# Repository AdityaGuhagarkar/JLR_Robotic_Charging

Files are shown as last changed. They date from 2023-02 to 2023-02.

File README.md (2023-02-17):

# JLR_Robotic_Charging

<!-- PROJECT DESCRIPTION -->

## Introduction:
The objective of this project was to develop a robotic arm that can automatically detect the vehicle's charging port and plug the socket into the charging port.

## Methodology:
<p>◦The CAD model of the robotic arm was developed using Fusion360 and SolidWorks. The Robotic arm simulation was done on MATLAB using the Kinova Gen3 Model for testing arm control algorithms.</p>
<p>◦For perception, a Yolov7 model was trained to detect the CCS2 charging port. Then, stereo cameras were used to determine the distance to the charding port. Finally an Aruco marker placed near the charging port was used to obtain the 6D pose.</p>
<p>◦For the given end pose, we create an inverse kinematics solver. To solve the inverse kinematics for each waypoint, we first obtain the target pose as a function of the waypoints and their orientations. The joint waypoints are then defined via the inverse kinematics function.</p>
<p>◦We have defined 4 ways to generate a trajectory, namely ‘trap’, ‘cubic’, ‘quintic’, and ‘bspline’</p>
<p>◦Then, we plot Velocity vs Time, Acceleration vs Time, Torque vs Time and Power vs Time via which we can find average power.</p>
<p>◦Torque is defined using the inverseDynamics function with the pose, velocity, acceleration and external forces as variables.</p>
<p>◦We finally visualize the robotic arm motion on a 3D plot</p>

## Robot Arm Design:

Objective:
To design a robotic arm that should be able to reach the charging port of the electric vehicle from the charging station with all the constraints as stated

Approach:
<p>Two different approaches have been taken to achieve the said objective</p>
◦Design_1: Design of a 6-DOF robotic arm <br>
◦Design_2 (alternate approach): Design of a 6-DOF robotic arm using pneumatically controlled artificial muscles for tough robotic applications <br>
<br>
<p>Design Specifications:</p>
◦DOF: 6 <br>
◦Mass: 54.2 kg <br>
◦Bounding box dimension: 0.16*0.7*0.17 (m) <br>
◦Payload: 5 kg <br>
◦Max. reach: 1.42 m <br>
◦Material: Al 6061 T6, PLA (3D printed shells for motor casing) <br>
<br>
MAIN MODEL
<br>
<p align="center">
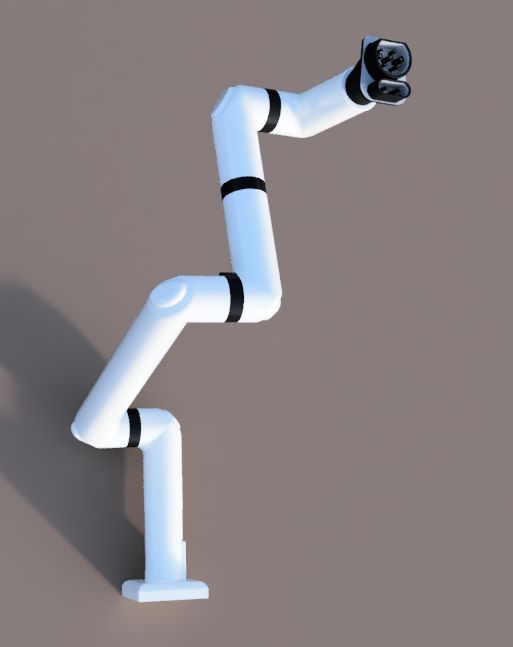
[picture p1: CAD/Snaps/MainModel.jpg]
  
</p>
<br>
ALTERNATE MODEL
<br>
<p align="center">
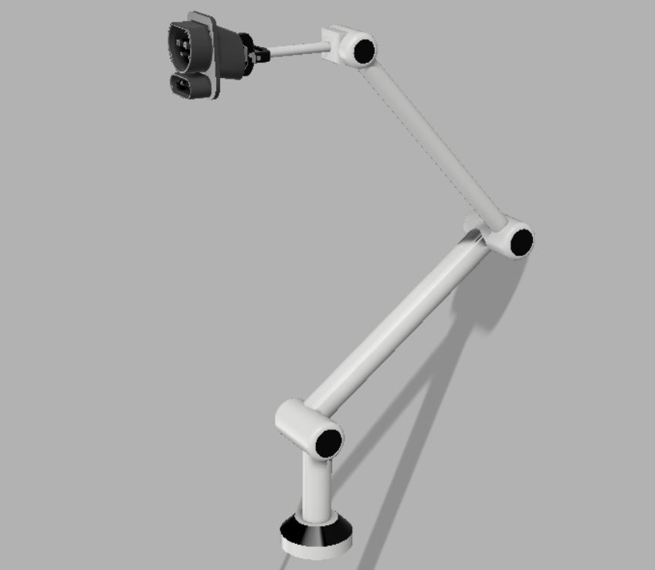
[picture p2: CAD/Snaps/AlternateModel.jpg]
  
</p>
<br>

## Bill of Materials
<p align="center">
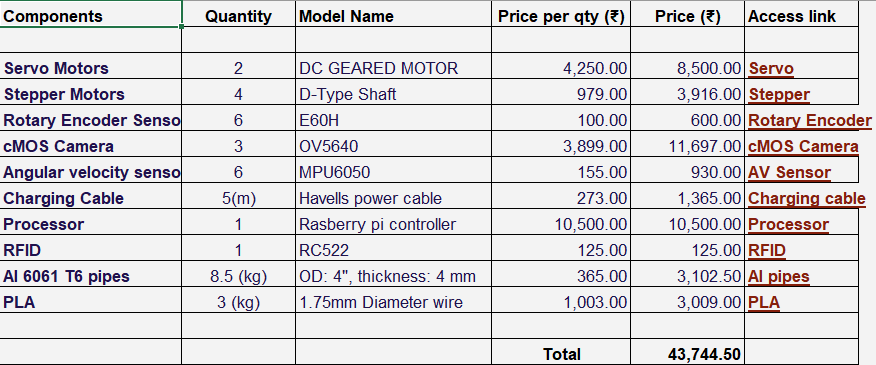
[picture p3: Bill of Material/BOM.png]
  
</p>

## Plots
<p align="center">
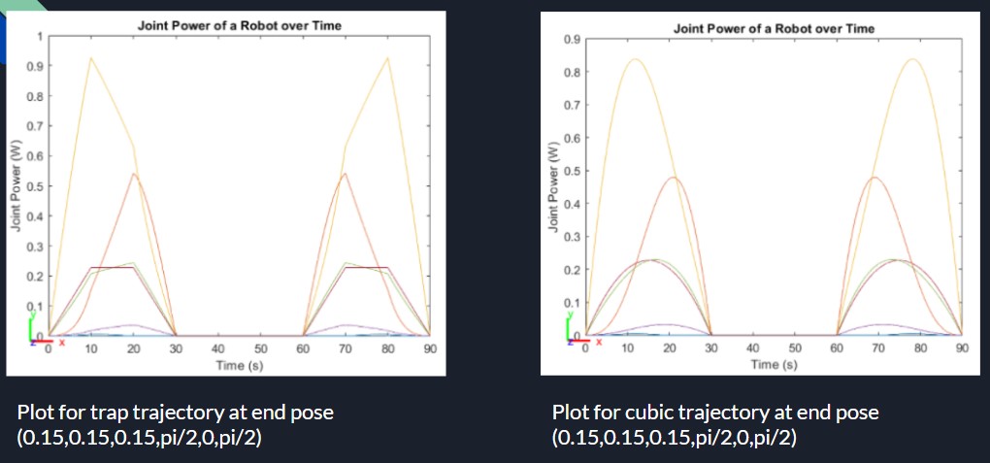
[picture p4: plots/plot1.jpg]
  
</p>
<p align="center">
  <img src="https://github.com/AdityaGuhagarkar/JLR_Robotic_Charging/blob/main/plots/plot2.jpg"">
</p>

## Conclusion:
The project was successful in designing a inexpensive Robotic Arm that can obtain the 6D pose of a CCS2 charging port and travel to a given 6D pose with the optimal trajectory. The breakthrough of the project was use the comparison of multiple trajectories to determine the most optimized one. In terms of the design the use of Pneumatic Artificial Muscles in the robotic arm end-effector is a major brakthrough as it is in-expensive and can carry 10 to 20 times the weight of a normal robotic hand.

## Installations
1) Install the MATLAB 2022b software
2) Download Fusion360 or SolidWorks to open the CAD model
3) ROS noetic

## Steps to run the code
1) Download the Robtic_Arm_Team53.mlx file and run it on the MATLAB 2022b software

## Contact Us

**Aditya Guhagarkar:**




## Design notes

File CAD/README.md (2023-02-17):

# Info related to CAD files

### There are two approaches taken to achieve the target stated in the problem statement

* This CAD folder contains two sub-folders, Main Model and Alternate Model
* Main Model contains the design of a 6-DOF robotic arm in .stp format on which all the simulations and testings have been performed
* Alternate Model contains the design of a robotic arm associated with artificial muscles for tough robotic applications in .stp format as a part of innovation of the project

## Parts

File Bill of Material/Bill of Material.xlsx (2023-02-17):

Components | Quantity | Model Name | Price per qty (₹) | Price (₹) | Access link
Servo Motors | 2 | DC GEARED MOTOR | 4250.00 | 8500.00 | Servo (https://robokits.co.in/motors/mega-torque-18v-250w-dc-motor/mega-torque-geared-18v-dc-motor/mega-torque-planetary-dc-geared-motor-250w-25rpm-18vdc)
Stepper Motors | 4 | D-Type Shaft | 979.00 | 3916.00 | Stepper (https://robu.in/product/5-5-kg-cm-nema-17-stepper-motor-4-wire-bipolar-cnc-3d-printer-robotics/)
Rotary Encoder Sensors | 6 | E60H | 100.00 | 600.00 | Rotary Encoder (https://www.tradeindia.com/products/e-60-series-encoder-8244740.html)
cMOS Camera | 3 | OV5640 | 3899.00 | 11697.00 | cMOS Camera (https://thinkrobotics.in/products/ov5640-5mp-usb-camera?variant=40097096171606&currency=INR)
Angular velocity sensor | 6 | MPU6050 | 155.00 | 930.00 | AV Sensor (https://robu.in/product/mpu-6050-gyro-sensor-2-accelerometer/)
Charging Cable | 5(m) | Havells power cable | 273.00 | 1365.00 | Charging cable (https://www.bestofelectricals.com/havells-25-sqmm-3-core-aluminium-armoured-power-cable)
Processor | 1 | Rasberry pi controller | 10500.00 | 10500.00 | Processor (https://www.indiamart.com/proddetail/raspberry-pi-4-model-b-8-gb-ram-controller-27556240055.html)
RFID | 1 | RC522 | 125.00 | 125.00 | RFID (https://robu.in/product/mifare-rfid-readerwriter-13-56mhz-rc522-spi-s50-fudan-card-and-keychain/)
Al 6061 T6 pipes | 8.5 (kg) | OD: 4", thickness: 4 mm | 365.00 | 3102.50 | Al pipes (https://www.indiamart.com/proddetail/aluminium-round-tube-6061-11473302391.html)
PLA | 3 (kg) | 1.75mm Diameter wire | 1003.00 | 3009.00 | PLA (https://roboticsdna.in/product/ducho-filla-pla-white-filaments-1kg-1-75mm-diameter/)
 |  |  | Total | 43744.50

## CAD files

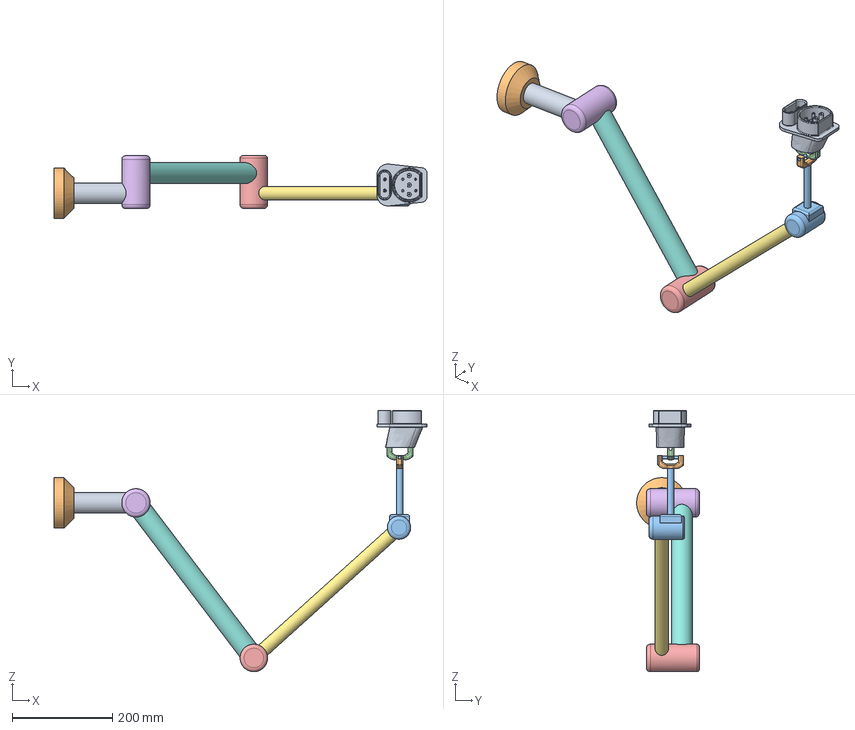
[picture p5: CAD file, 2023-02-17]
CAD/Alternate Model/Team_53_Alternate_CAD.step
745.1 x 125.4 x 522.2 mm

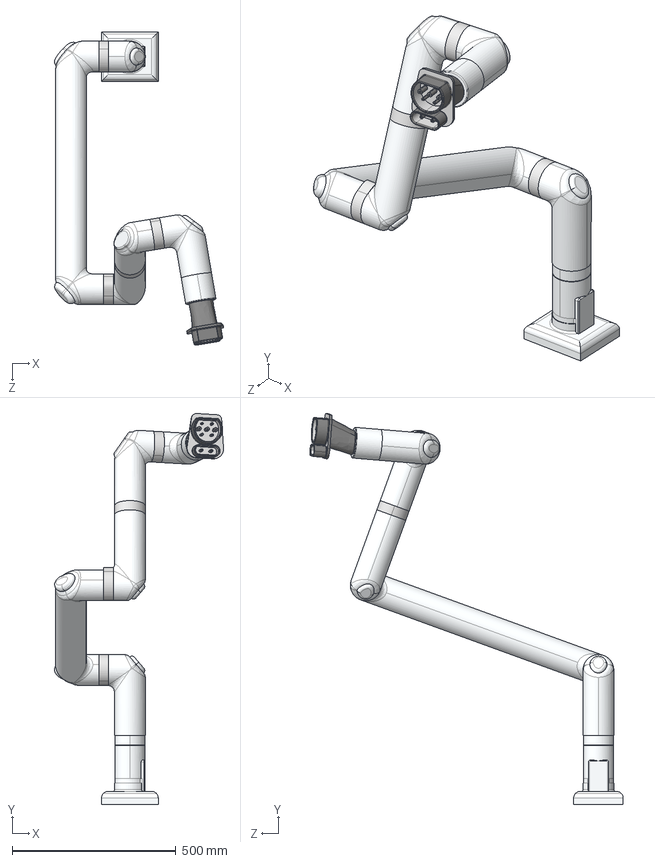
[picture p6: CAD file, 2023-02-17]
CAD/Main Model/Team53_CAD.STEP
515.8 x 1192.6 x 955.7 mm
Component2.step
Component3.step
Component4.step
Component5.step
Component6.step
Component7.step
Component11.step
Component12.step
Component13.step
Component14.step
charger1 v1.step
GEN3 SIMPLIFIED Base v2.step

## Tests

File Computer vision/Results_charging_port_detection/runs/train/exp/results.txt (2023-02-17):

      0/54     9.86G   0.07363   0.01738         0     0.091         7       640   0.08563    0.1429   0.01824  0.002435   0.07714   0.01471         0
      1/54     10.5G   0.07008   0.01523         0   0.08531         8       640     0.421    0.1905    0.1765   0.08131   0.05993   0.01324         0
      2/54     10.5G   0.06129   0.01396         0   0.07526         4       640    0.5985    0.2842    0.3169    0.1961   0.05192   0.01178         0
      3/54     10.5G   0.05545   0.01294         0    0.0684         4       640    0.6415    0.4286    0.4471      0.19   0.04723   0.01094         0
      4/54     10.5G   0.05784   0.01223         0   0.07007         8       640     0.444    0.7605    0.5216    0.2603   0.04609  0.009817         0
      5/54     10.5G   0.05266   0.01195         0   0.06461         9       640    0.6915    0.8095    0.7795     0.325   0.04038  0.009511         0
      6/54     10.5G   0.05031   0.01075         0   0.06106         6       640    0.9797    0.4286    0.6627    0.3163   0.04025  0.008527         0
      7/54     10.5G   0.04858   0.01234         0   0.06092        10       640    0.7334    0.8095    0.8091     0.367   0.04064  0.007933         0
      8/54     10.5G   0.04538   0.01045         0   0.05583         3       640    0.9933    0.8571    0.8968    0.4347   0.03926   0.00739         0
      9/54     10.5G    0.0476  0.009854         0   0.05745         9       640    0.5996         1    0.8546    0.3736   0.04401  0.006465         0
     10/54     10.5G   0.04744  0.009395         0   0.05683         9       640    0.8928    0.8571    0.9156    0.3467   0.04612  0.005987         0
     11/54     10.5G   0.04975  0.009401         0   0.05915         8       640    0.9999    0.7619    0.9254    0.5961   0.04062  0.006147         0
     12/54     10.5G    0.0518  0.009531         0   0.06133        10       640    0.5707    0.9524    0.6934    0.1999   0.04377  0.006101         0
     13/54     10.5G    0.0514  0.008499         0    0.0599         6       640    0.7809    0.8571    0.9105    0.3316   0.03931  0.006681         0
     14/54     10.5G   0.04867  0.009162         0   0.05783         5       640    0.9492    0.9048    0.9515    0.6098   0.03764  0.006175         0
     15/54     10.5G   0.05104  0.008408         0   0.05945         8       640    0.8058         1    0.9441    0.4369   0.04134  0.005695         0
     16/54     10.5G   0.05093  0.008919         0   0.05985        10       640    0.8678    0.9524    0.9547    0.5338   0.03601  0.005875         0
     17/54     10.5G   0.05103  0.008557         0   0.05959         7       640    0.8678    0.9524    0.9482    0.6928   0.03335  0.005712         0
     18/54     10.5G   0.04794  0.007934         0   0.05588         6       640    0.9995    0.8571    0.9756    0.6514   0.03446  0.005881         0
     19/54     10.5G   0.04854  0.008346         0   0.05689         9       640    0.9116         1    0.9663    0.5097    0.0337  0.005956         0
     20/54     10.5G   0.04844  0.008044         0   0.05648        14       640    0.9439    0.8571    0.9261    0.3649   0.03865  0.005925         0
     21/54     10.5G   0.04678   0.00759         0   0.05437         6       640    0.4587    0.2857    0.2444    0.1007   0.05786  0.006718         0
     22/54     10.5G    0.0453  0.006785         0   0.05209         9       640    0.8885     0.381     0.415      0.26    0.0499  0.006329         0
     23/54     10.5G    0.0534  0.007368         0   0.06077         8       640    0.9285    0.6188    0.7659    0.4457   0.03375  0.006239         0
     24/54     10.5G   0.05385  0.007485         0   0.06134         9       640    0.9997    0.9048     0.968    0.6455   0.03087  0.005296         0
     25/54     10.5G   0.03771  0.007555         0   0.04526         9       640         1         1     0.995    0.6494   0.03046  0.004872         0
     26/54     10.5G   0.04801  0.006845         0   0.05485         8       640     0.954         1    0.9846    0.5905   0.03055  0.004811         0
     27/54     10.5G   0.04689  0.007624         0   0.05452        14       640    0.9992         1     0.995     0.642   0.03101   0.00471         0
     28/54     10.5G   0.04463  0.006933         0   0.05156         7       640    0.9997         1     0.995    0.6303    0.0305   0.00452         0
     29/54     10.5G   0.04432  0.006531         0   0.05086         7       640    0.9999         1     0.995    0.7365   0.02671  0.004793         0
     30/54     10.5G   0.04034   0.00665         0   0.04699         8       640    0.9532         1    0.9864    0.7612   0.02703  0.004733         0
     31/54     10.5G   0.04444  0.006424         0   0.05086         9       640    0.9999         1     0.995    0.6927   0.03045  0.004254         0
     32/54     10.5G   0.04678  0.006623         0   0.05341         9       640    0.9999         1     0.995    0.7903   0.02812   0.00406         0
     33/54     10.5G   0.03863  0.006629         0   0.04526        11       640    0.9985         1     0.995    0.5573   0.03192  0.003997         0
     34/54     10.5G   0.04646  0.006467         0   0.05292         6       640    0.9539         1    0.9846    0.6494   0.02955  0.003956         0
     35/54     10.5G   0.03707  0.005843         0   0.04292         8       640     0.913         1    0.9763    0.6163   0.02843  0.004009         0
     36/54     10.5G   0.04627   0.00642         0   0.05269         7       640    0.9952         1     0.995    0.5451   0.03082  0.004045         0
     37/54     10.5G   0.04173  0.006325         0   0.04805         6       640     0.913         1    0.9872    0.5966   0.03011  0.004021         0
     38/54     10.5G   0.04822  0.006426         0   0.05464        10       640    0.9125         1    0.9785    0.5951   0.02812  0.004088         0
     39/54     10.5G   0.03724  0.006459         0    0.0437         6       640    0.8398         1     0.967    0.5938    0.0274  0.004216         0
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

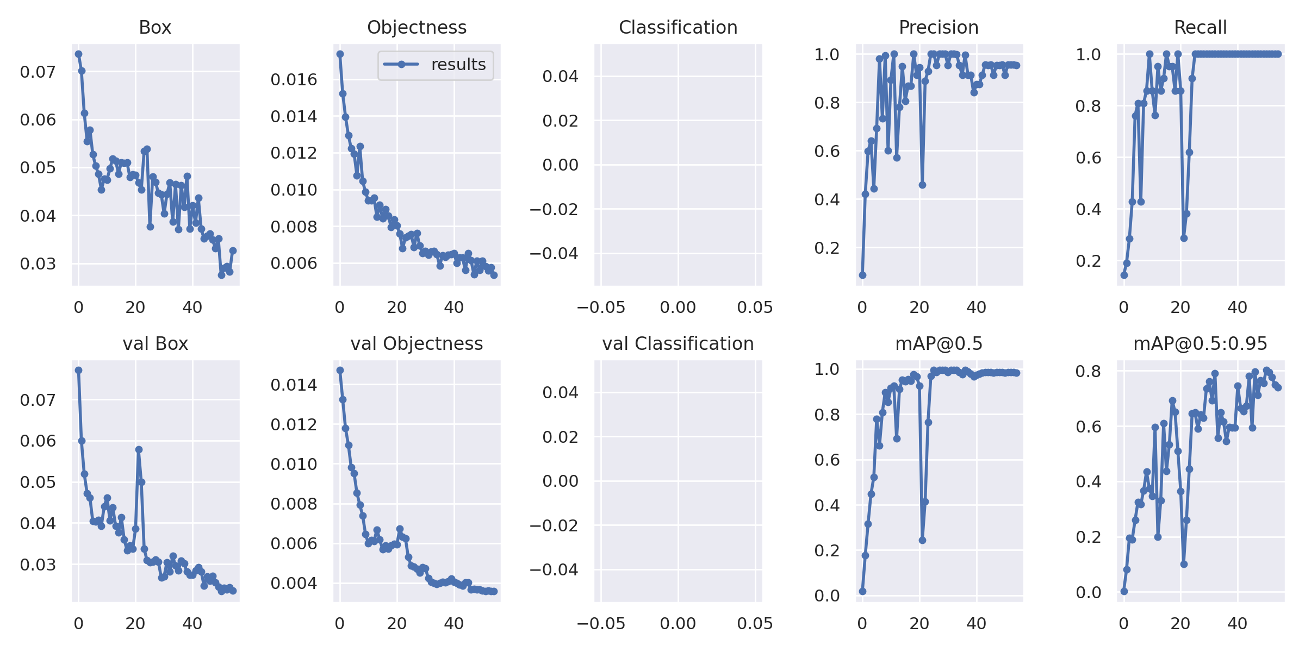
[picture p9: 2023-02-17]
Computer vision/Results_charging_port_detection/runs/train/exp/results.png

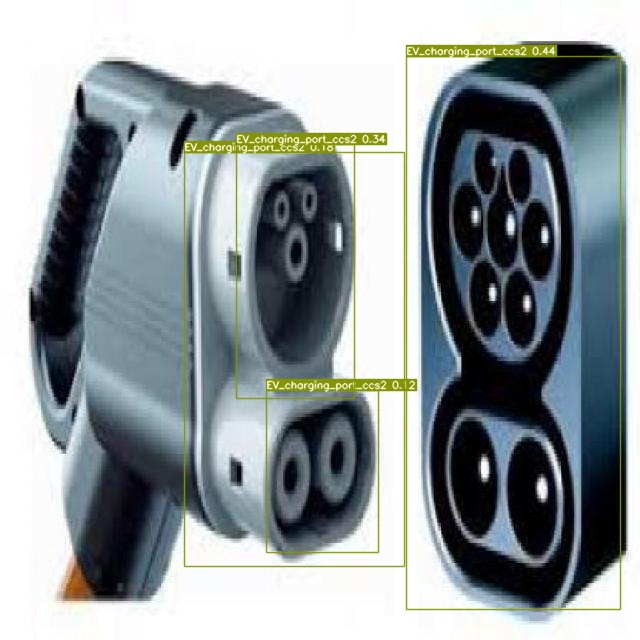
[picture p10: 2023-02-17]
Computer vision/Results_charging_port_detection/runs/detect/exp/images_jpg.rf.e9e7e6fc1a2ba773d080f938fb97bf27.jpg

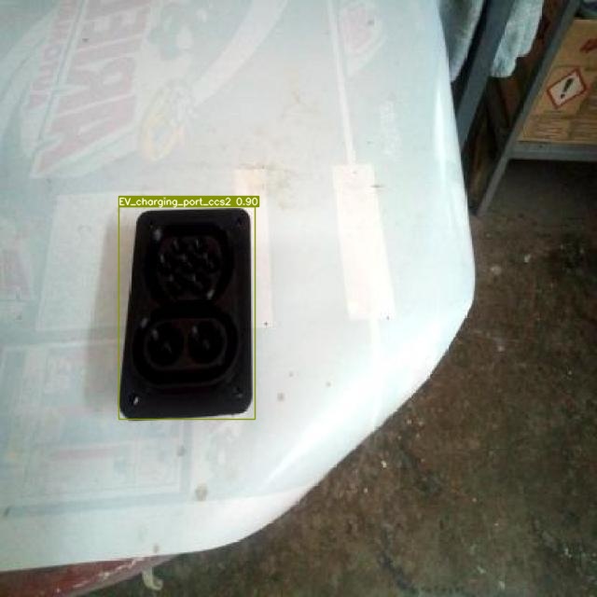
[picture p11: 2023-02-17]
Computer vision/Results_charging_port_detection/runs/detect/exp/IMG_20210816_190515_jpg.rf.1dbb269175961f5886dbdfcece61e45b.jpg

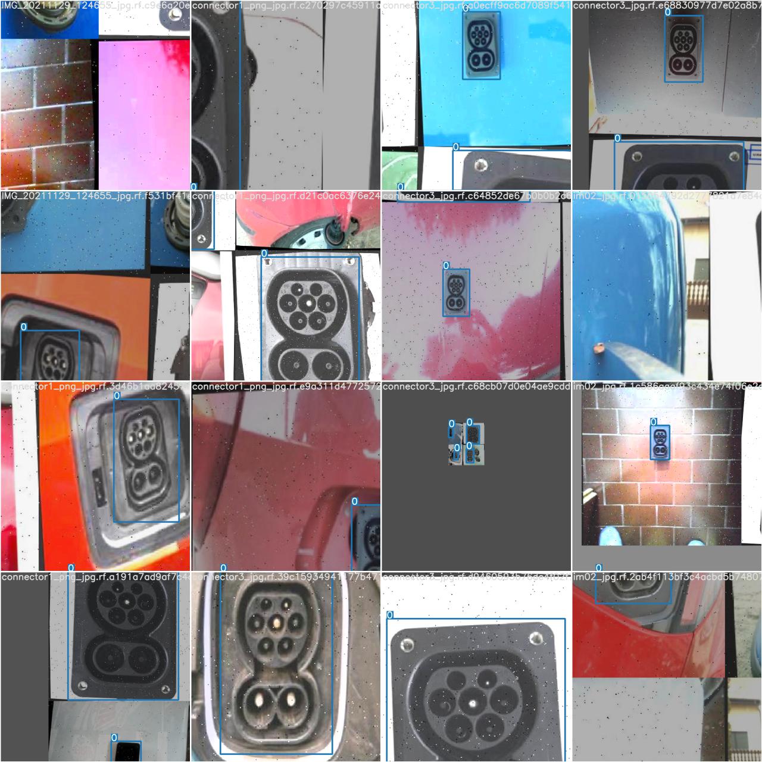
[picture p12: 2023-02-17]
Computer vision/Results_charging_port_detection/runs/train/exp/train_batch7.jpg
